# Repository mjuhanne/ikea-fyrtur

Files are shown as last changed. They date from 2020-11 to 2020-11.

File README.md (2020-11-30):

# ikea-fyrtur

## Introduction

This is a ESP8266 WiFi module PCB to be used with Ikea Fyrtur or Kadrilj roller blinds. It substitutes the original Ikea Trådfri (Zigbee) based board.

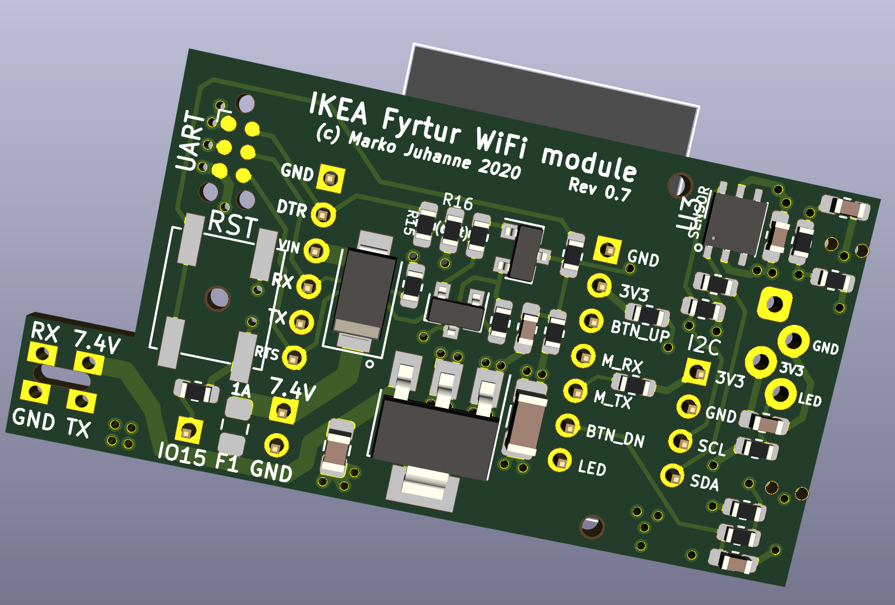
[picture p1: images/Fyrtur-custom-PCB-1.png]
Ikea Fyrtur custom PCB image 1

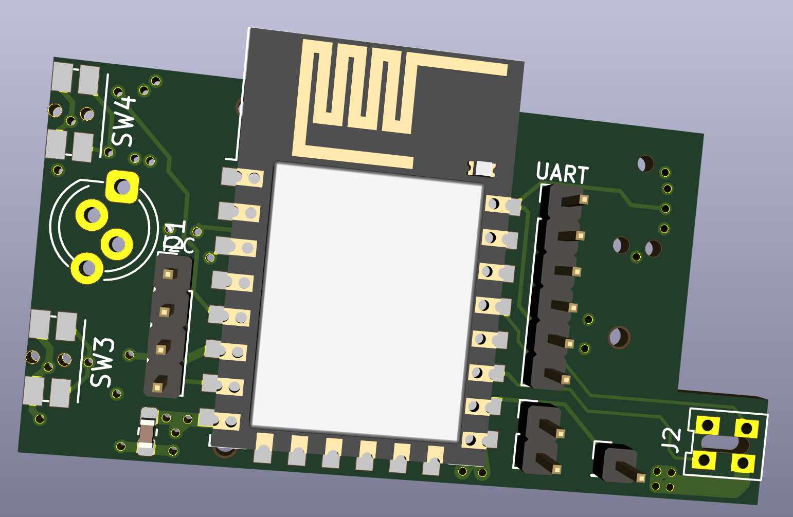
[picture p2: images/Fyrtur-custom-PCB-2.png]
Ikea Fyrtur custom PCB image 2


#### Enhancements:
 - Easier and more stable connectivity with non-Ikea home automation systems (such as Home Assistant) without additional hardware hub (please see [esp-fyrtur repository](https://github.com/mjuhanne/fyrtur-esp) for the software)
 - Designed to be powered with wired 5-7.5V DC power adapter, so no more charging the battery every few months! (5V charger can be used only when a custom fyrtur motor firmware is used. For this, see [fyrtur-motor-board repository](https://github.com/mjuhanne/fyrtur-motor-board))
 - On-board 1A fuse for extra safety
 - Additional connection header allows the use of other platforms (such as ESP32 or Arduino) since now the battery compartment is empty and can hold larger wireless modules
 - Optional I2C Temperature and humidity sensor (Si7021 or HTU21D)
 - Optional Neopixel RGB-led to be used as a status LED

## Assembly
 
Ready Gerber and BOM/component position files for PCB production and SMT assembly for JLCPCB.com
 - The tiny motor connector PCB should be desoldered from the original board and re-used.
 - The only self-sourced components are the ESP12F module, temperature sensor and fuse (The buttons and LED can be ordered or alternatively scavenged from the original board)

## Programming

Programming can be done via the 2mm pitch UART header using FTDI adapter. Alternatively a special [TagConnect](https://www.tag-connect.com/product/tc2030-nl-ftdi-ttl-232r-usb-to-tc2030-no-legs-serial-cable) adapter can be used if you don't want to solder the UART header (not tested yet).

## Interface board

 The PCB can also be used as a plain interface board (with buttons and LED populated, with optional temperature sensor). In this case only the following components are needed:
 
#### Connector header:
  - J1 EXT_CTRL (1x7, 2mm pitch) (or solder female Dupont wires directly to the header)

#### Buttons and debounce circuitry:
 - Panasonic right angle tactile switches (EVQ-P7L01P)
 - R11,R12 (10K)
 - R9 (120R), R10 (10K)
 - C6, C7 (100nF)

#### LED:
 - any 3.5mm diameter LED
 - R13 (270R - 1K, depending on the LED forward voltage drop and desired brightness)

#### Temperature sensor components:
 - U3 (SI7021 / HTU21D)
 - R6, R4 (10k)
 - C5 (100nF)
 - J6 I2C header (1x4, 2mm pitch) (or solder female Dupont wires directly to the header)

### Example wiring for ESP32 (DevKitC V4)
  - J1:1 <--> GND
  - J1:2 <--> 3V3
  - J1:3 <--> D21 (BTN_UP)
  - J1:4 <--> D5 (Motor UART RX)
  - J1:5 <--> D23 (Motor UART TX)
  - J1:6 <--> D22 (BTN_DOWN)
  - J1:7 <--> D18 (LED)
 
#### Optional I2C temperature sensor:
  - J6:3 <--> D19 (SCL)
  - J6:4 <--> D13 (SDA)

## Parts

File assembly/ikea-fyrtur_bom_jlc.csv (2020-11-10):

Comment | Designator | Footprint | LCSC Part #
22uF 25V | C1 | C_0805_2012Metric_Pad1.15x1.40mm_HandSolder | C45783
47uF 10V | C3 | C_1206_3216Metric_Pad1.42x1.75mm_HandSolder | C96123
100nF 50V | C4,C7,C6,C2,C5,C8 | C_0603_1608Metric_Pad1.05x0.95mm_HandSolder | C14663
SS14 | D2 | D_SMA | C2480
SS8050-G | Q1,Q2 | SOT-23 | C2150
10K | R1,R2,R3,R5,R7,R4,R11,R12,R6,R8 | R_0603_1608Metric | C25804
1K | R10,R13 | R_0603_1608Metric | C21190
120R | R9 | R_0603_1608Metric | C22787
470R | R14,R17 | R_0603_1608Metric | C23179
0R | R15 | R_0603_1608Metric | C21189
AMS1117-3.3 | U1 | SOT-223-3_TabPin2 | C6186

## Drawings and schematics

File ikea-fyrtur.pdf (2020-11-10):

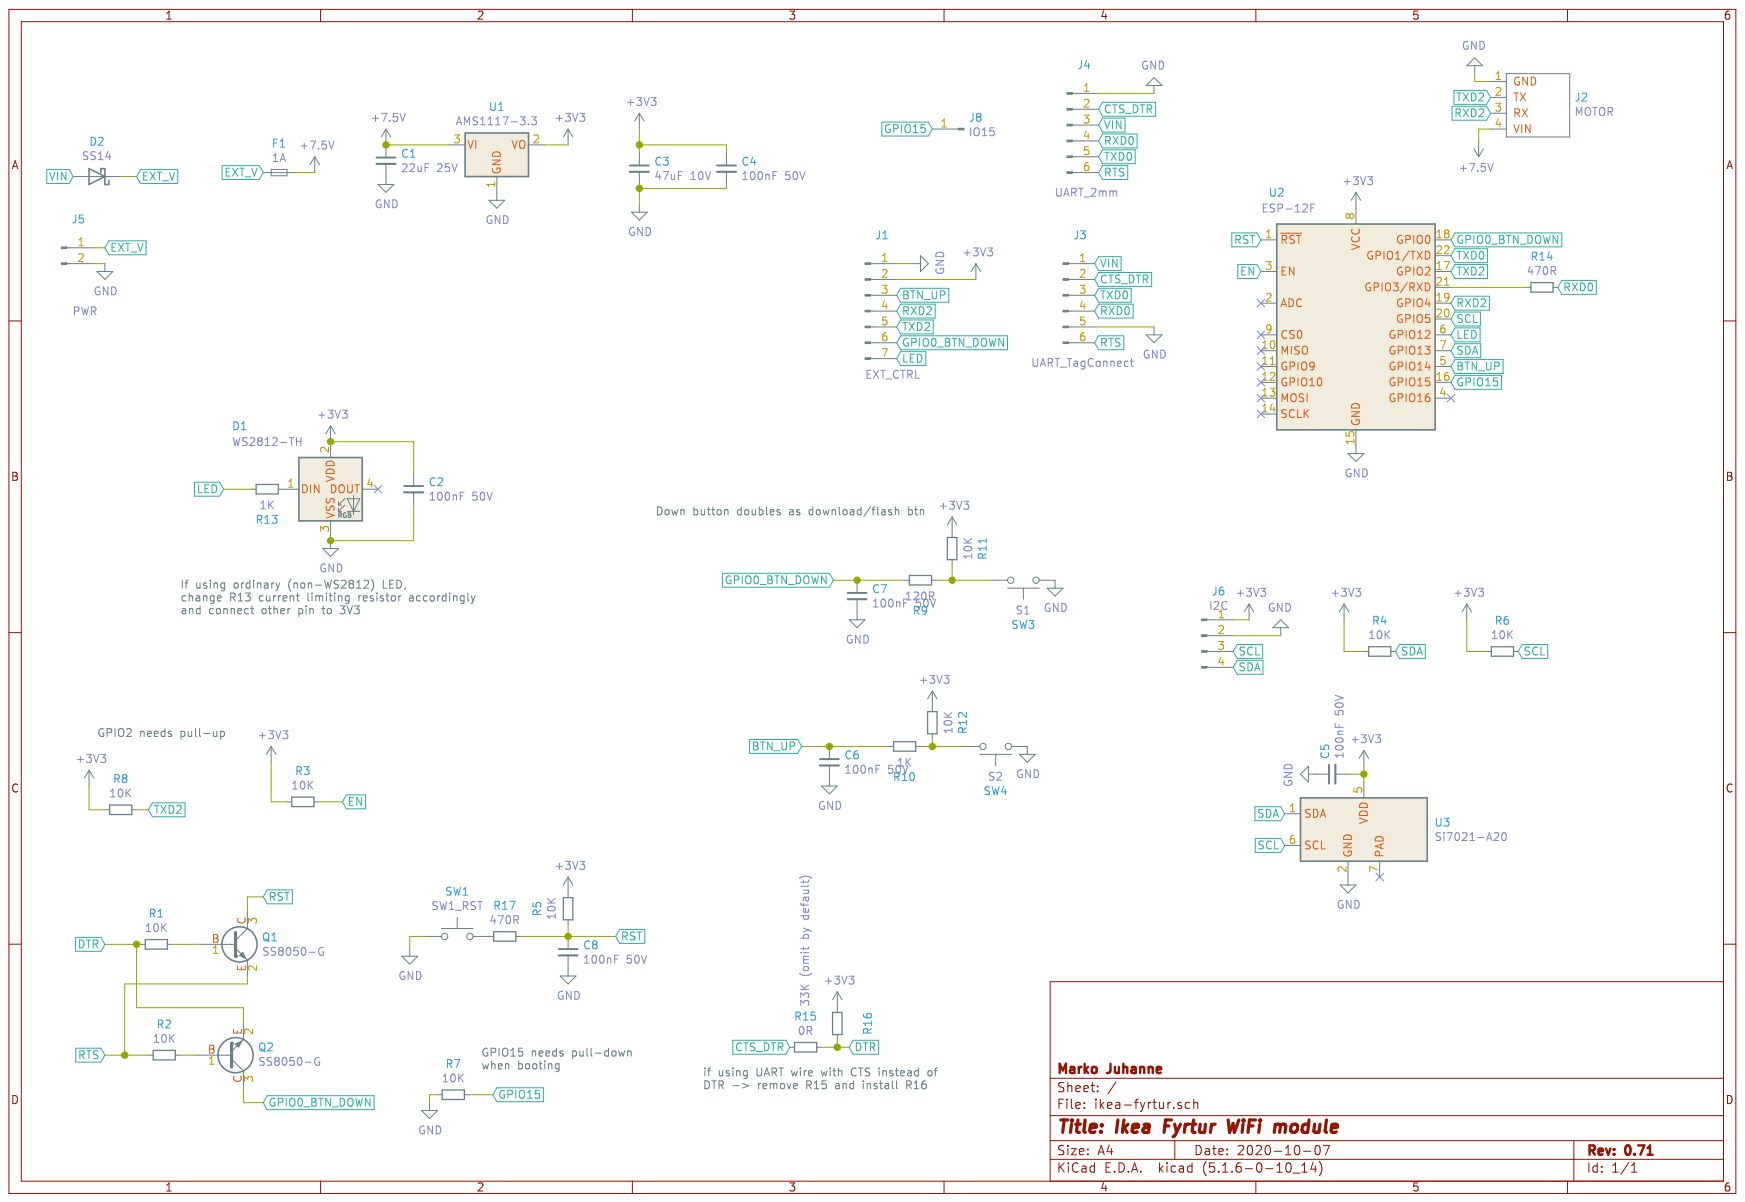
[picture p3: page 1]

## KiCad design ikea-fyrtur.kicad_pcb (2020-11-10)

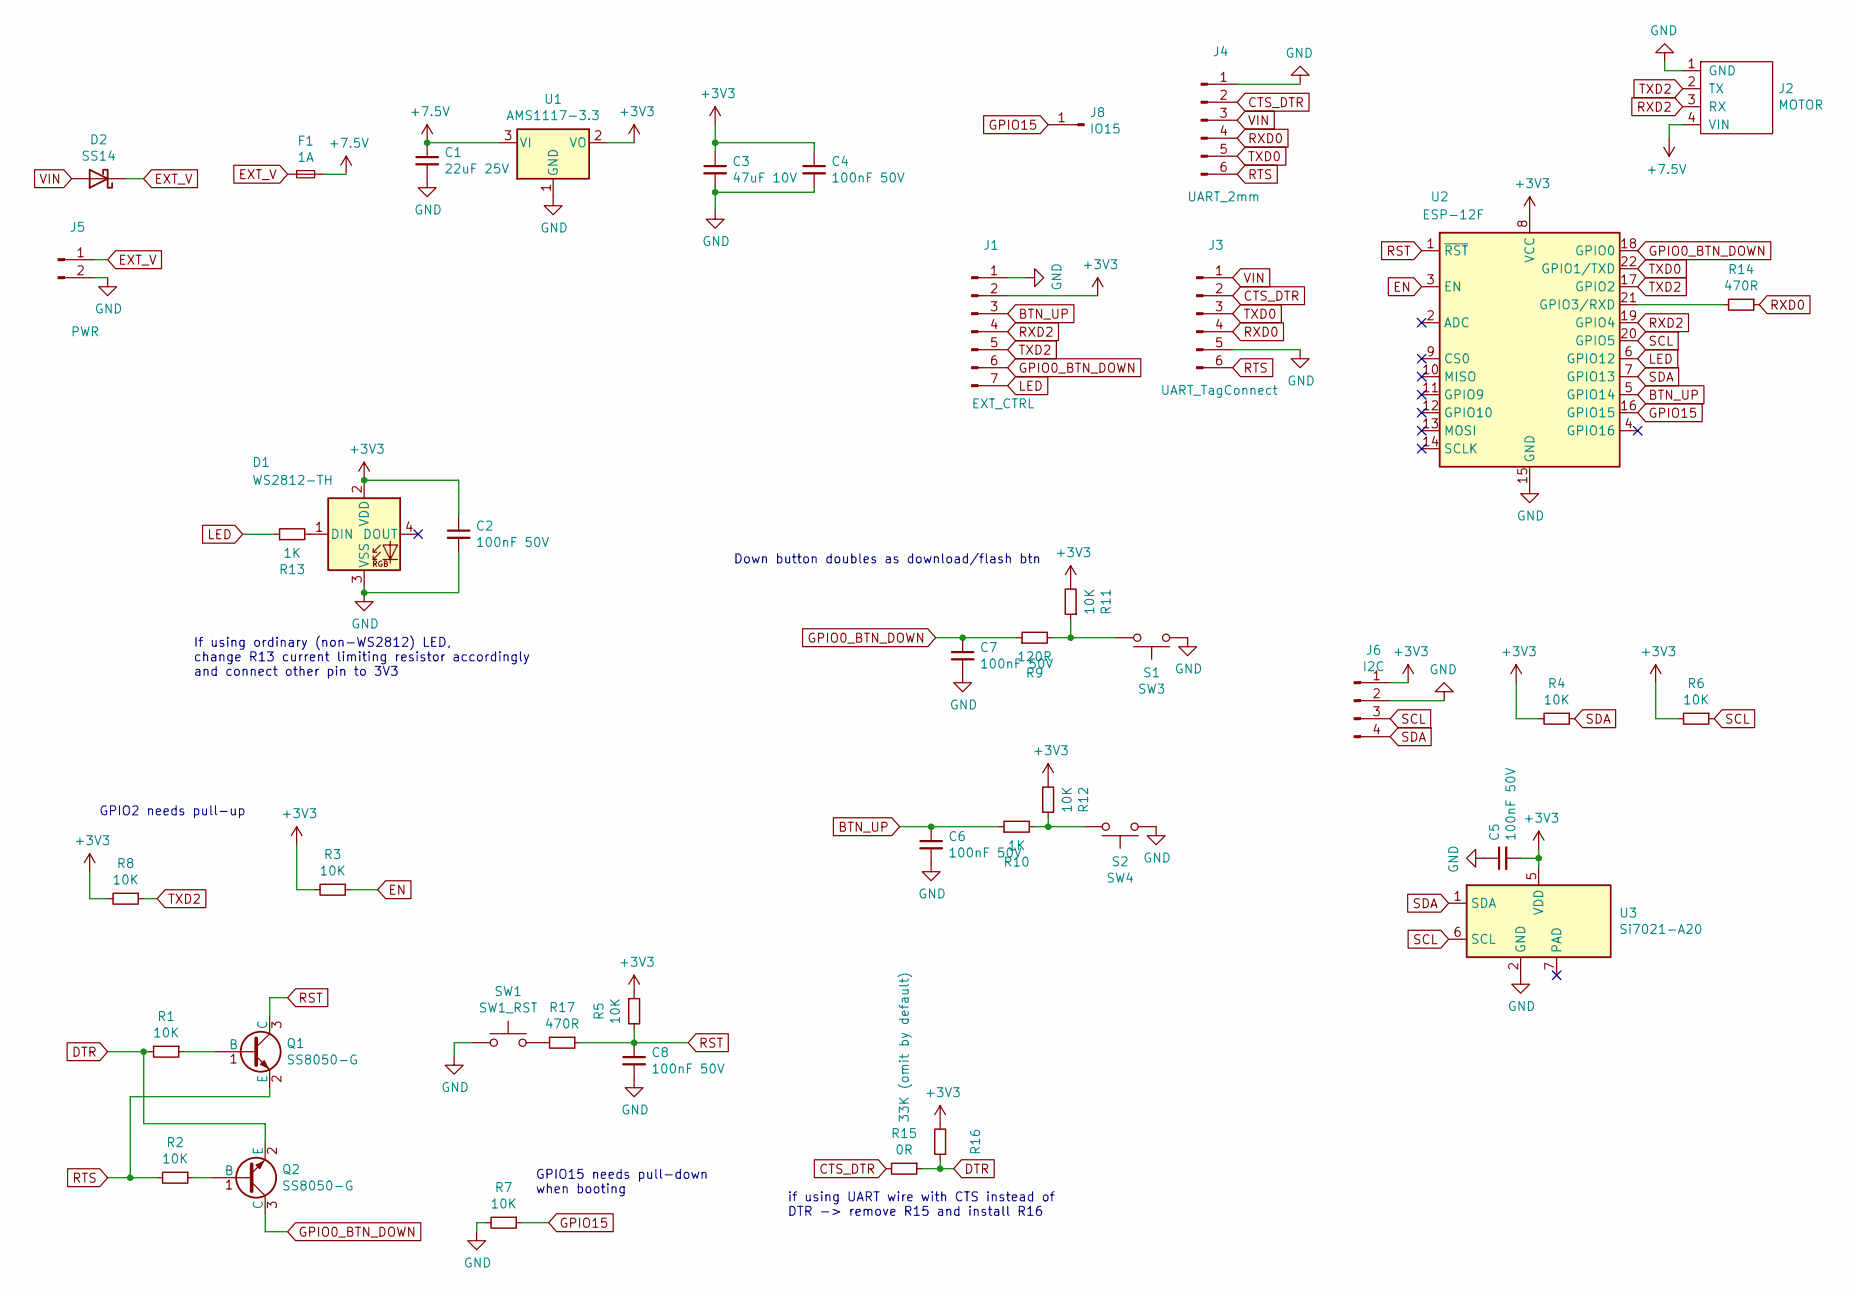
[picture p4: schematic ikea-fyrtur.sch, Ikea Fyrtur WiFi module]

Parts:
C1: 22uF 25V; C_0805_2012Metric_Pad1.15x1.40mm_HandSolder; LCSC Part C45783
C2, C4, C5, C6, C7, C8: 100nF 50V; C_0603_1608Metric_Pad1.05x0.95mm_HandSolder; LCSC Part C14663
C3: 47uF 10V; C_1206_3216Metric_Pad1.42x1.75mm_HandSolder; LCSC Part C96123
D1: WS2812-TH; JLCPCB BOM 0
D2: SS14; D_SMA; LCSC Part C2480
F1: 1A; Fuse_0805_2012Metric_Pad1.15x1.40mm_HandSolder; JLCPCB BOM 0
J1: EXT_CTRL; PinHeader_1x07_P2.00mm_Vertical; JLCPCB BOM 0
J2: MOTOR; Fyrtyr-Motor-Connector; JLCPCB BOM 0
J3: UART_TagConnect; Tag-Connect_TC2030-IDC-NL_2x03_P1.27mm_Vertical; JLCPCB BOM 0
J4: UART_2mm; PinHeader_1x06_P2.00mm_Vertical; JLCPCB BOM 0
J5: PWR; PinHeader_1x02_P2.00mm_Vertical; JLCPCB BOM 0
J6: I2C; PinHeader_1x04_P2.00mm_Vertical; JLCPCB BOM 0
J8: IO15; PinHeader_1x01_P2.00mm_Vertical; JLCPCB BOM 0
Q1, Q2: SS8050-G; SOT-23; LCSC Part C2150
R1, R2, R3, R4, R5, R6, R7, R8, R11, R12: 10K; R_0603_1608Metric; LCSC Part C25804
R9: 120R; R_0603_1608Metric; LCSC Part C21190
R10, R13: 1K; R_0603_1608Metric; LCSC Part C21190
R14, R17: 470R; R_0603_1608Metric; LCSC Part C23179
R15: 0R; R_0603_1608Metric; LCSC Part C21189
R16: 33K (omit by default); R_0603_1608Metric; JLCPCB BOM 0
SW1: SW1_RST; SW_SPST_EVQP0; JLCPCB BOM 0
SW3: S1; Panasonic_EVQ-P7L; JLCPCB BOM 0
SW4: S2; Panasonic_EVQ-P7L; JLCPCB BOM 0
U1: AMS1117-3.3; SOT-223-3_TabPin2; LCSC Part C6186
U2: ESP-12F; ESP-12E; JLCPCB BOM 0
U3: Si7021-A20; DFN-6-1EP_3x3mm_P1mm_EP1.5x2.4mm-HS; JLCPCB BOM 0

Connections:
+3V3: C2.1, C3.1, C4.1, C5.2, D1.2 (VDD), J1.2, J6.1, R3.2, R4.2, R5.1, R6.2, R8.2, R11.2, R12.2, R16.2, U1.2 (VO), U2.8 (VCC), U3.5 (VDD)
+7.5V: C1.1, F1.2, J2.4 (VIN), U1.3 (VI)
BTN_UP: C6.1, J1.3, R10.1, U2.5 (GPIO14)
CTS_DTR: J3.2, J4.2, R15.2
DTR: Q2.2 (E), R1.2, R15.1, R16.1
EN: R3.1, U2.3 (EN)
EXT_V: D2.1 (K), F1.1, J5.1
GND: C1.2, C2.2, C3.2, C4.2, C5.1, C6.2, C7.2, C8.2, D1.3 (VSS), J1.1, J2.1 (GND), J3.5, J4.1, J5.2, J6.2, R7.2, SW1.1, SW3.1, SW4.1, U1.1 (GND), U2.15 (GND), U3.2 (GND)
GPIO0_BTN_DOWN: C7.1, J1.6, Q2.3 (C), R9.1, U2.18 (GPIO0)
GPIO15: J8.1, R7.1, U2.16 (GPIO15)
LED: J1.7, R13.1, U2.6 (GPIO12)
unnamed: D1.1 (DIN), R13.2
unnamed: Q1.1 (B), R1.1
unnamed: Q2.1 (B), R2.1
unnamed: R10.2, R12.1, SW4.2
unnamed: R9.2, R11.1, SW3.2
unnamed: R14.2, U2.21 (GPIO3/RXD)
unnamed: R17.2, SW1.2
RST: C8.1, Q1.3 (C), R5.2, R17.1, U2.1 (~RST)
RTS: J3.6, J4.6, Q1.2 (E), R2.2
RXD0: J3.4, J4.4, R14.1
RXD2: J1.4, J2.3 (RX), U2.19 (GPIO4)
SCL: J6.3, R6.1, U2.20 (GPIO5), U3.6 (SCL)
SDA: J6.4, R4.1, U2.7 (GPIO13), U3.1 (SDA)
TXD0: J3.3, J4.5, U2.22 (GPIO1/TXD)
TXD2: J1.5, J2.2 (TX), R8.1, U2.17 (GPIO2)
VIN: D2.2 (A), J3.1, J4.3

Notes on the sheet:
Down button doubles as download/flash btn
if using UART wire with CTS instead of DTR -> remove R15 and install R16
GPIO2 needs pull-up
GPIO15 needs pull-down when booting
If using ordinary (non-WS2812) LED, change R13 current limiting resistor accordingly and connect other pin to 3V3

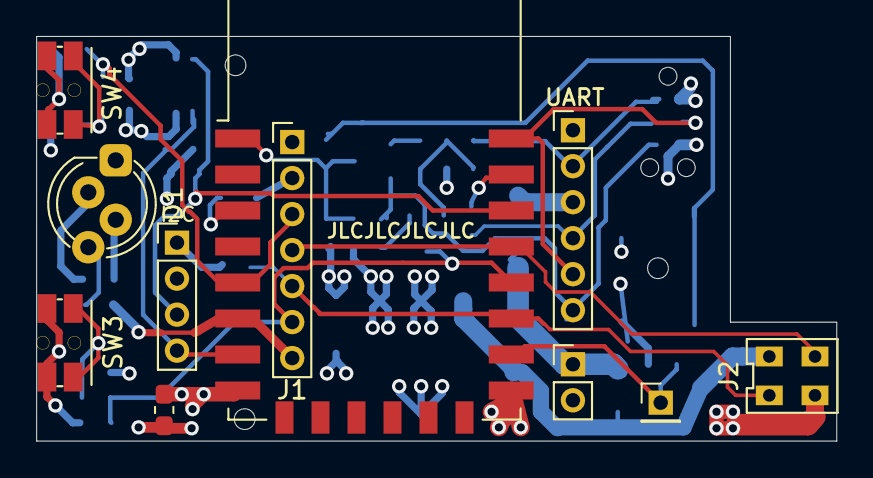
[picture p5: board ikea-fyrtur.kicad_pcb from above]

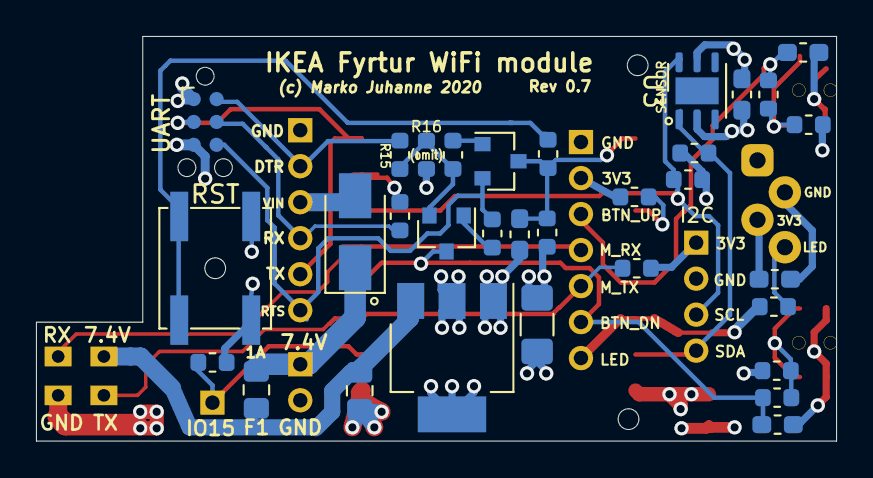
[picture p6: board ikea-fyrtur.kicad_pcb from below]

Board: 4 copper layers, 44.5 x 22.5 mm, 43 parts (32 on the bottom side), 27 nets.

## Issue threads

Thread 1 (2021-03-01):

Add explanation on which files go to JCPCB

carlos-sarmiento, 2021-03-01:
I'm interested in using this project with my Fyrtur blinds. I've worked with electronics (soldering and programming) but I've never ordered a custom PCB board.

It would be super useful to have some instructions on how to order the boards from JCPCB. Even better if there was a place we could buy the already built board (and get you some money for the hard work)

mjuhanne, 2021-03-09:
Hi, sorry for the delayed response.

I really recommend watching Phil's video (https://www.youtube.com/watch?v=t5phi3nT8OU&t=6s) that inspired also me to develop STM32 boards and order them assembled from JLCPCB. It's a really long video (2,5 hours!) and worth watching entirely, but if you just want to know about the assembly files and ordering, skip to around 2:18:00
Basically you just need to send the gerber files (zipped) and the assembly files (which parts are needed and their positioning), and then check on their web based preview tool that they are correctly positioned.

That being said, at this point long after ordering the PCBs myself and testing them both with ESP8266 and ESP32, I would not bother with the custom PCB anymore. Instead with my 2 last blinds I just removed the Zigbee module from the original Ikea PCB and soldered wires to external ESP32 DevkitC V4 module which is situated at the battery compartment.
Pros:
 - ESP32 has more memory and is more stable (especially when launching its own Access Point with the WIFI/MQTT configuration portal)
 - The next update of ESP32 firmware will have possibility to do OTA update of the STM32 motor module. ESP8266 does not have enough memory to do this
 - I might add SSL support for MQTT connection later, for more secure home networking. Again, ESP8266 does not have enough memory for this.
Cons:
  - More fragile if wires are soldered directly to the Zigbee module pads

rubin110, 2022-03-18:
Sorry for resurrecting this thread. I don't have a hot air rework station, nor do I have good experience doing rework like this. Pretty sure I'm going to butcher the board if I attempt desoldering the zigbee module by hand through a braid or solder sucker. Is there a version of this board I can order with an ESP32?

Also how many layers is this board, this is the first time I'm ordering a custom board and am a bit clueless. Thank you.

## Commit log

2020-11-10 - Change R9 from 1K to 120R (Setting GPIO0 line low via Down-Button may not lower voltage enough otherwise) - Added images, updated README - Change schematic revision to 0.71 (Resistor value change d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
    [ikea-fyrtur.kicad_pcb, ikea-fyrtur.sch, ikea-fyrtur_bom_jlc.csv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]
2020-11-10 Add schematic PDF and update README
